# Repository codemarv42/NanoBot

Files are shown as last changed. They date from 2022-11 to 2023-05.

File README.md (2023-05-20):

# NanoBot

The NanoBot is basically a small robot, which was developed for educational purposes. It comes with a variety of sensors such as light sensors, color sensors, distance sensors and with the paired Jetson Nano from Nvidia with one or more cameras. In addition, you can connect even more modules and sensors through the extra pins, making the limits almost infinite. 

NanoBotRev1

# Hardware

The hardware of this project consists of a self-developed circuit board and 3D printed parts made of TPE 60A and PLA. 

## Short building instruction

### Note that only the first version of the NanoBot board works without problems, so it is not recommended to rebuild the latest version!

The assembly of the robot requires **extensive equipment and experience** in soldering SMD components. How you solder the components is up to you.

Recommended tools:

- Flat tip soldering iron
- Solder (0.8mm), flux
- Hotplate
- Hot air soldering station
- Solder paste (SnAg3Cu0.5)
- Tweezers, side cutter

The required components are listed in the Excel document in the hardware folder and are mostly from LCSC. The board itself can be produced by different manufacturers, for example JLCPCB. Simply upload the Gerber file and select the following parameters:

Parameter for PCB (NanoBot REV1):

- Layer: 2
- Thickness: 1,6mm / 2mm
- Length: 112.9mm
- Height: 100.8mm
- Minimum Copper Trace Width: 0.15mm

Parameter for PCB (NanoBot REV2):

- Layer: 2
- Thickness: 1,6mm / 2mm
- Length: 112.9mm
- Height: 100.8mm
- Minimum Copper Trace Width: 0.15mm

## 3D printed parts

For better light measurements, it is recommended to print out the three different light guards and attach them with superglue. Also, use TPE 60A for the tires, as this elastic material prevents the robot from slipping on the floor, unlike TPU.

Parts: 
- ***4x Flange coupling connector 3mm (not 3d printed!)***
- 4x Motor bracket PLA (40% infill)
- 1x light sensor protection Resin (Black)
- 2x Outer light sensor protection Resin (Black)
- 4x Tire TPE 60A
- 1x Rotary encoder knob TPU / TPE
- 4x Rim PLA

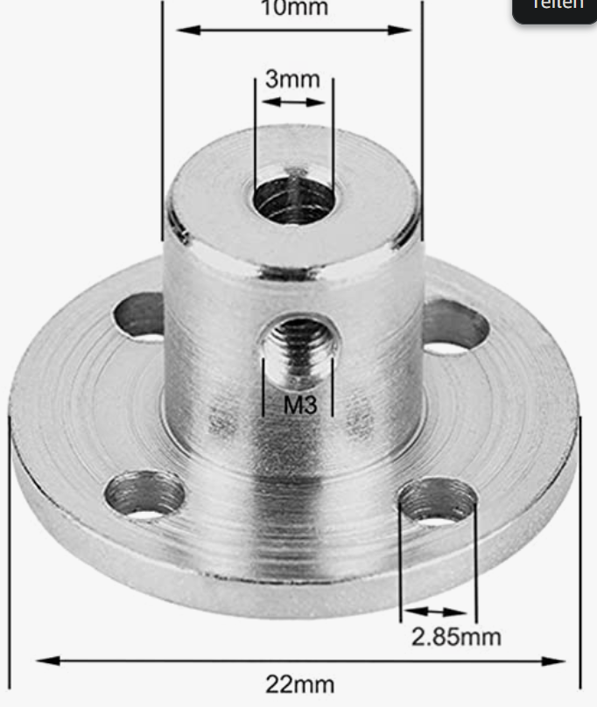
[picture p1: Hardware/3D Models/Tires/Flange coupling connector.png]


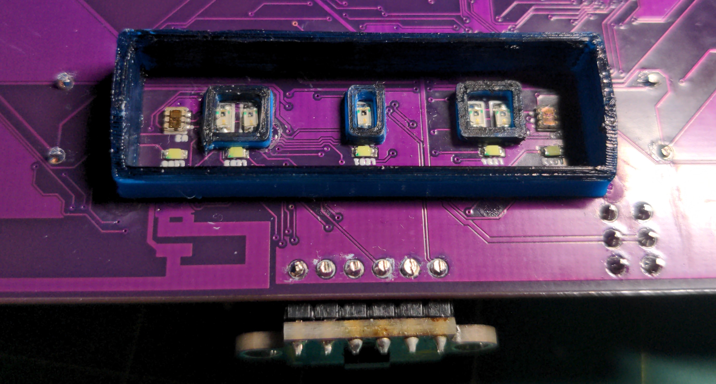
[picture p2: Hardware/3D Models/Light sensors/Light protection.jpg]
Light protector


## Improvements

> - [ ] Place light sensors in the center to increase maneuverability
> - [ ] Bigger Tires
> - [X] Better XT-30 position on the PCB
> - [X] More external ports
> - [X] Internal Li-Po charger, which draws power via USB-C PD
> - [X] Physical switch or MOSFET to disconnect the battery from the PCB
> - [X] Battery under discharge protection
> - [X] Additional light sensors on the outside of the PCB
> - [X] Constant motor voltage
> - [ ] Jetson Nano power supply with short circuit protection
> - [X] Material reflective sensor on the bottom
> - [X] Use Led with a wider spectrum
> - [X] Esd and insulation around gyro sensor
> - [ ] Reset button does not work
> - [X] Mounting holes next to the light sensor bar and the silver strip sensor

Nano Bot REV2

# Software

In my case, the robot is used to follow a line, avoid obstacles on the track and collect balls. These are the requirements for RoboCup in the Rescue Line division. However, depending on the requirements of the robot, the code will vary in your case. Therefore, this code serves mainly as a basis for your application. However, the code contains everything in the overall package to control and read out all sensors and peripherals. You can also reprogram the robot with Micro Python, because the processor (ESP32) allows it.

Required libraries:

- Adafruit_GFX.h - https://github.com/adafruit/Adafruit-GFX-Library
- Adafruit_SSD1306.h - https://github.com/adafruit/Adafruit_SSD1306
- ESP32_Servo.h - https://github.com/jkb-git/ESP32Servo
- MPU6050_light.h - https://github.com/rfetick/MPU6050_light
- CD74HC4067.h - https://github.com/waspinator/CD74HC4067
- VL53L1X.h - https://github.com/pololu/vl53l1x-arduino
- Adafruit_TCS34725.h - https://github.com/adafruit/Adafruit_TCS34725
- Adafruit_BusIO - https://github.com/adafruit/Adafruit_BusIO

## USB driver

In some cases, the USB controller is not automatically detected, which means that you have to install an additional driver:

- https://www.silabs.com/developers/usb-to-uart-bridge-vcp-drivers?tab=downloads

## Compilation settings

To compile your own program and then upload it to the NanoBot, some steps are necessary:

1. First you have to install the kernel of the ESP32 in Arduino: https://docs.espressif.com/projects/arduino-esp32/en/latest/installing.html
2. Next, the compilation settings must be specified. To do this, first select "ESP32 Dev Module" under Tools --> Board.
3. In the last step, the parameters of the ESP32 on the NanoBot must be set. To do this, select the following under Tools: 
- Board: "ESP32 Dev Module"
- Upload Speed: "921600"
- CPU Frequency: "240MHz (WiFi/BT)"
- Flash Frequency: "80MHz"
- Flash Mode: "QIO"
- Flash Size: "16MB (128Mb)" **4MB if you installed the W25Q32JVZPIQ Flash**
- Partition Scheme: "Minimal SPIFFS (1.9MB APP with OTA/190KB SPIFFS)" **for smaller code: Default**
- Programmer: "AVRISP mkll"
- Erase all flash: "Disabled"

## Improvements

> - [ ] Develop a communication protocol for the ESP32 and Jetson Nano via the I2C pin

## Flash BIN files to the robot

- Download the flash tool: https://www.espressif.com/en/support/download/other-tools
- Unzip the downloaded ZIP file and copy the selected BIN file into the bin folder contained in the unzipped file
- Start the exe file and select esp32
- Press the upper first box and then select the path of the bin file
- write next to the "@": 0x10000
- Then connect the robot to the pc and select the correct COM port (If the COM port is not displayed, install the driver)
- Click on start und press the boot button on the robot, if the upload does not start (If the boot button is not present, bridge the two pads with the name: "BOOT" and "GND")

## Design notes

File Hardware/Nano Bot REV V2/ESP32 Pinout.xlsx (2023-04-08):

GPIO | Input | Output | Belegt mit | Hinweis
0 | (OK) | (OK) | 0-BOOT | outputs PWM signal at boot
1 | X | (OK) | / | debug output at boot
2 | OK | OK | 2-P_ON | LED
3 | (OK) | X | / | HIGH at boot
4 | OK | OK | 4-S0
5 | OK | OK | 5-S1 | outputs PWM signal at boot
6 | X | X | / | connected to the integrated SPI flash
7 | X | X | / | connected to the integrated SPI flash
8 | X | X | / | connected to the integrated SPI flash
9 | X | X | / | connected to the integrated SPI flash
10 | X | X | / | connected to the integrated SPI flash
11 | X | X | / | connected to the integrated SPI flash
12 | (OK) | OK | 12-S2 | boot fail if pulled high
13 | OK | OK | 13-S3
14 | OK | OK | 14-CHARGE_STAT | outputs PWM signal at boot
15 | OK | OK | 15-ENC_SW | outputs PWM signal at boot
16 | OK | OK | 16
17 | OK | OK | 17-EN_RST
18 | OK | OK | 18-SERVO2
19 | OK | OK | 19-SERVO1
21 | OK | OK | 21-SDA
22 | OK | OK | 22-SCL
23 | OK | OK | 23-PWMA
25 | OK | OK | 25-PWMB
26 | OK | OK | 26-BUZZER
27 | OK | OK | 27-SHCP
32 | OK | OK | 32-STCP
33 | OK | OK | 33-DS
34 | OK | X | 34-ENC_B
35 | OK | X | 35-ENC_A
36 | OK | X | 36-VBAT | ADC
39 | OK | X | 39-VOUT | ADC

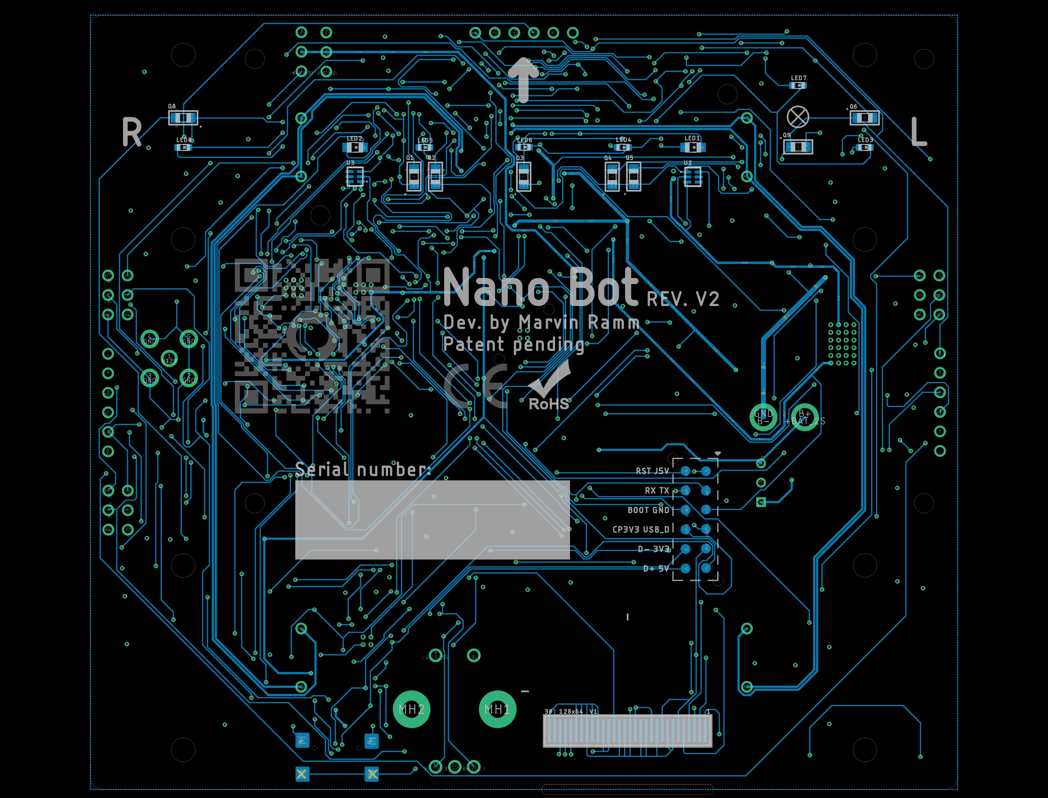
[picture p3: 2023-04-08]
Hardware/Nano Bot REV V2/NanoBot_6.png

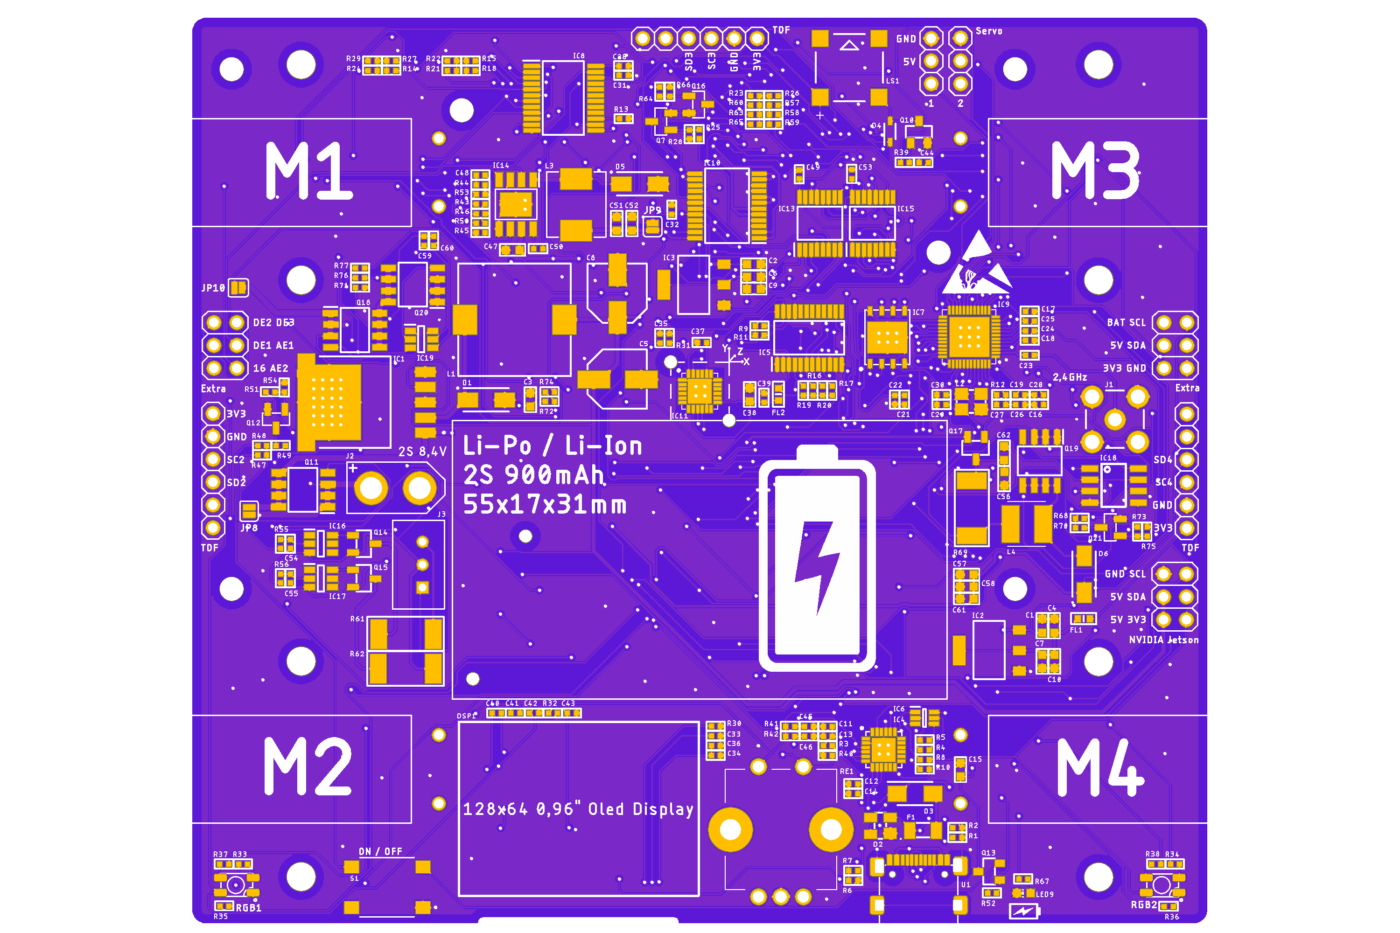
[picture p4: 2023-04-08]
Hardware/Nano Bot REV V2/NanoBot_1.png

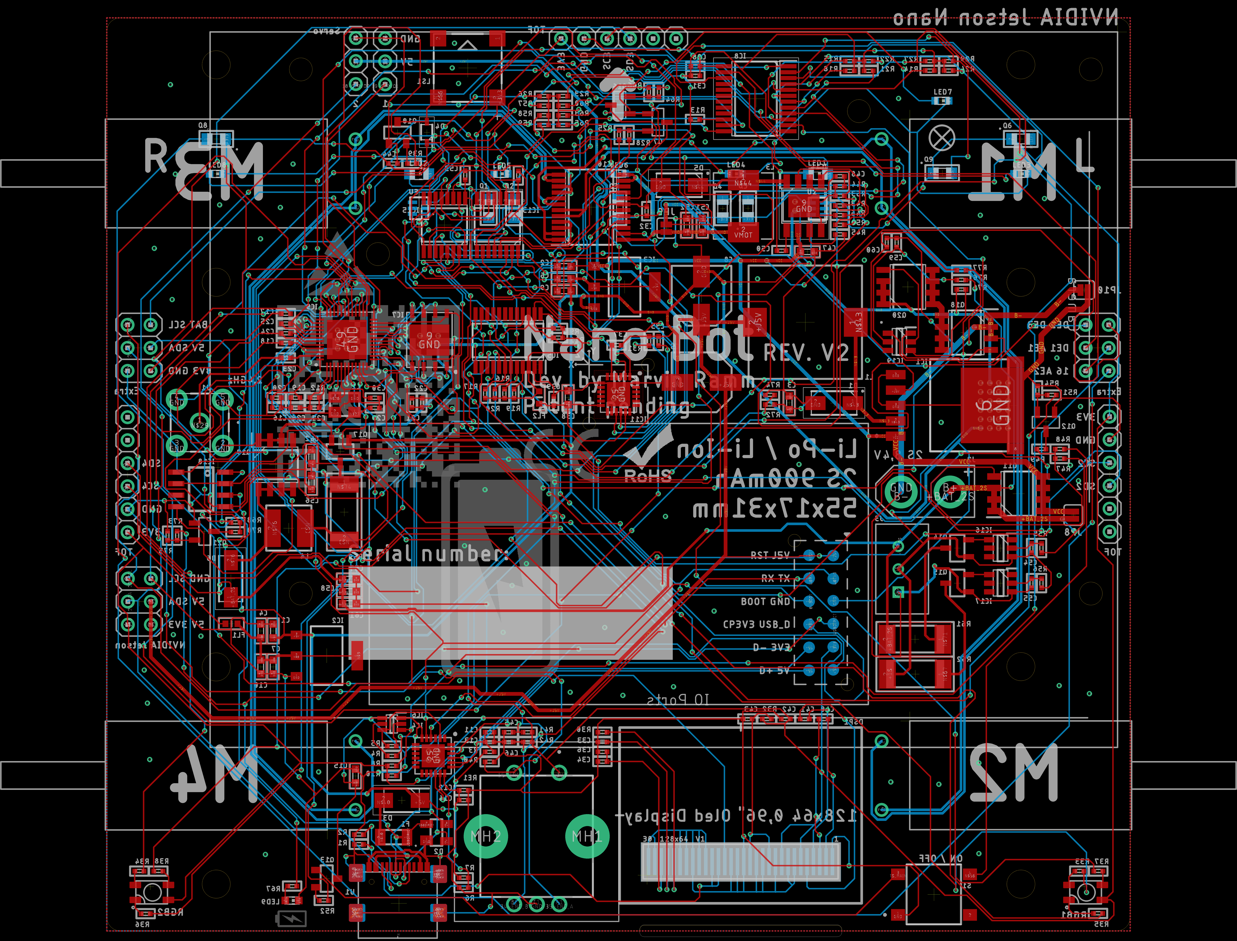
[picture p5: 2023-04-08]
Hardware/Nano Bot REV V2/NanoBot_4.png

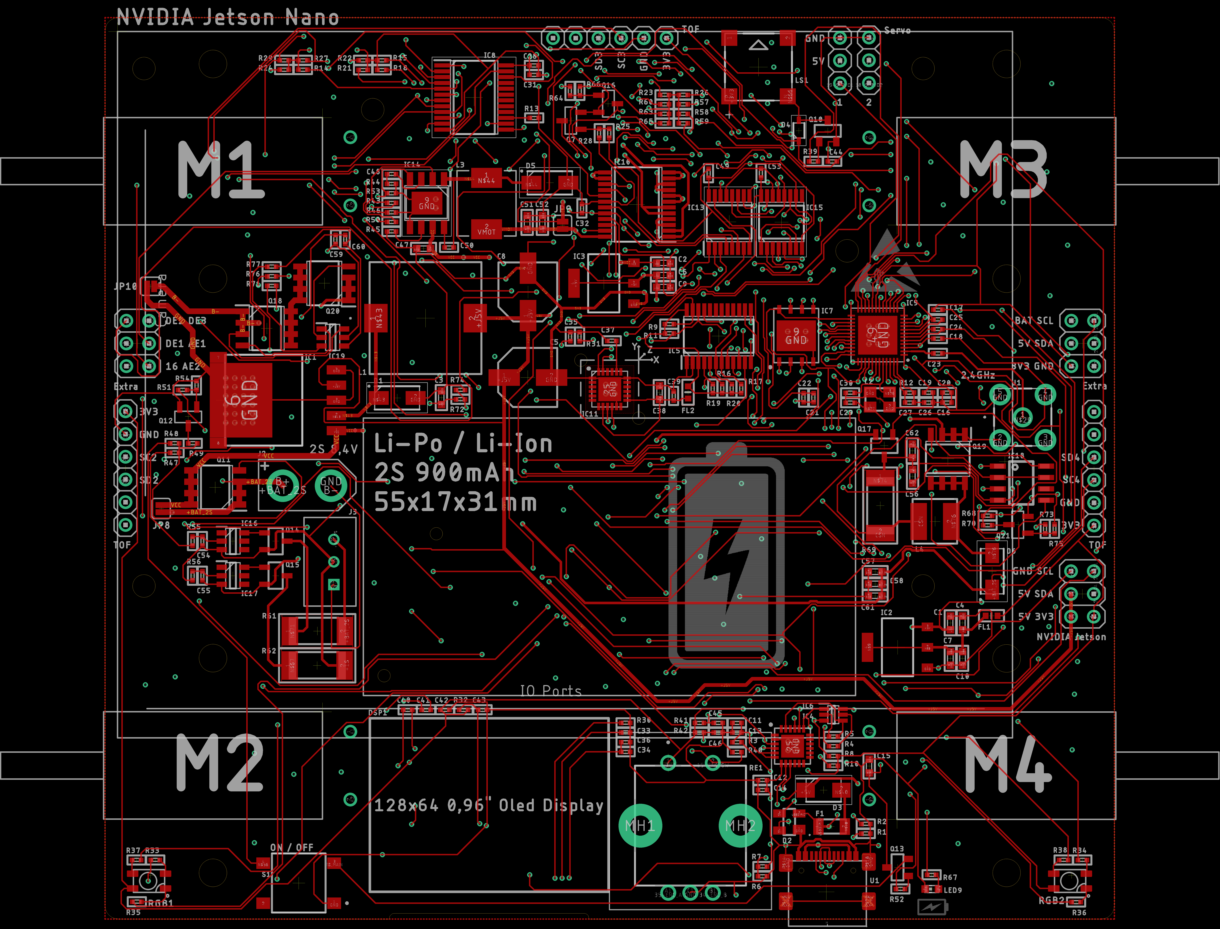
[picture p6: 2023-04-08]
Hardware/Nano Bot REV V2/NanoBot_5.png

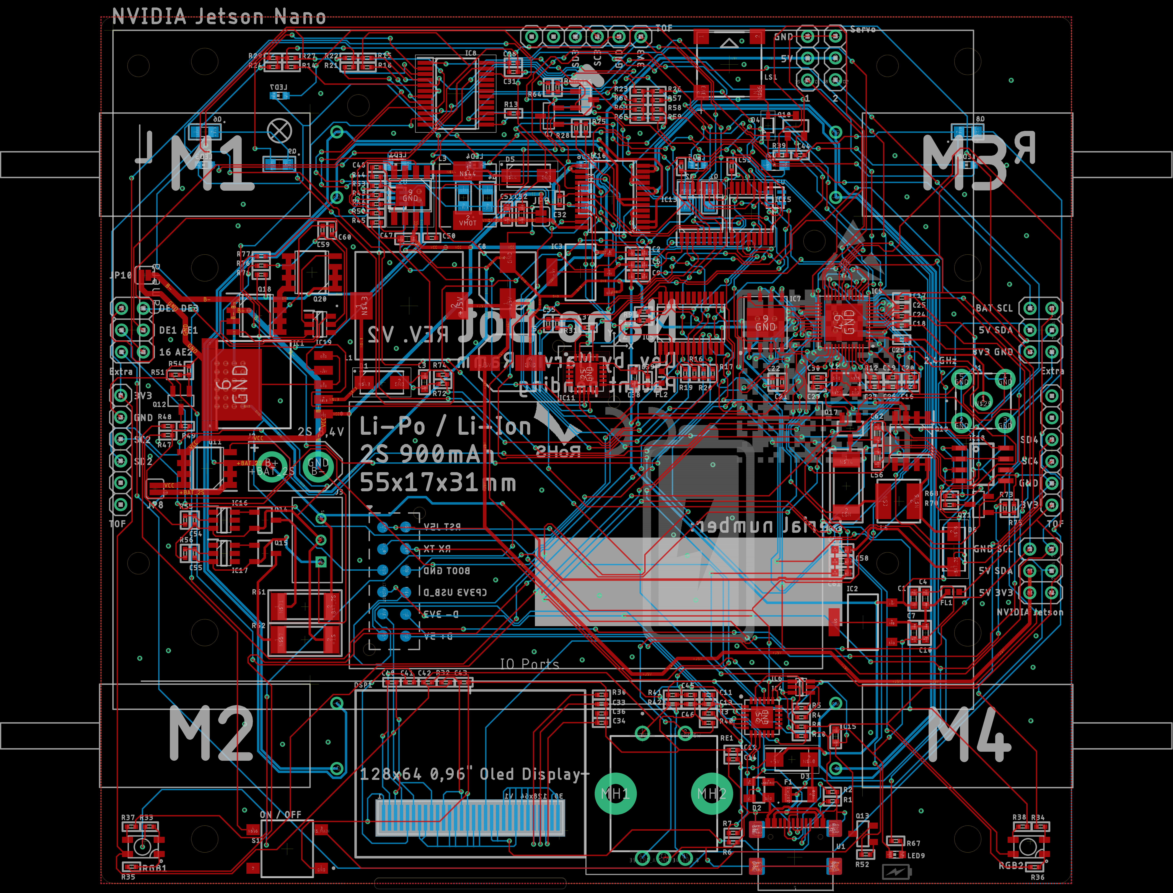
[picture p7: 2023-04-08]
Hardware/Nano Bot REV V2/NanoBot_3.png

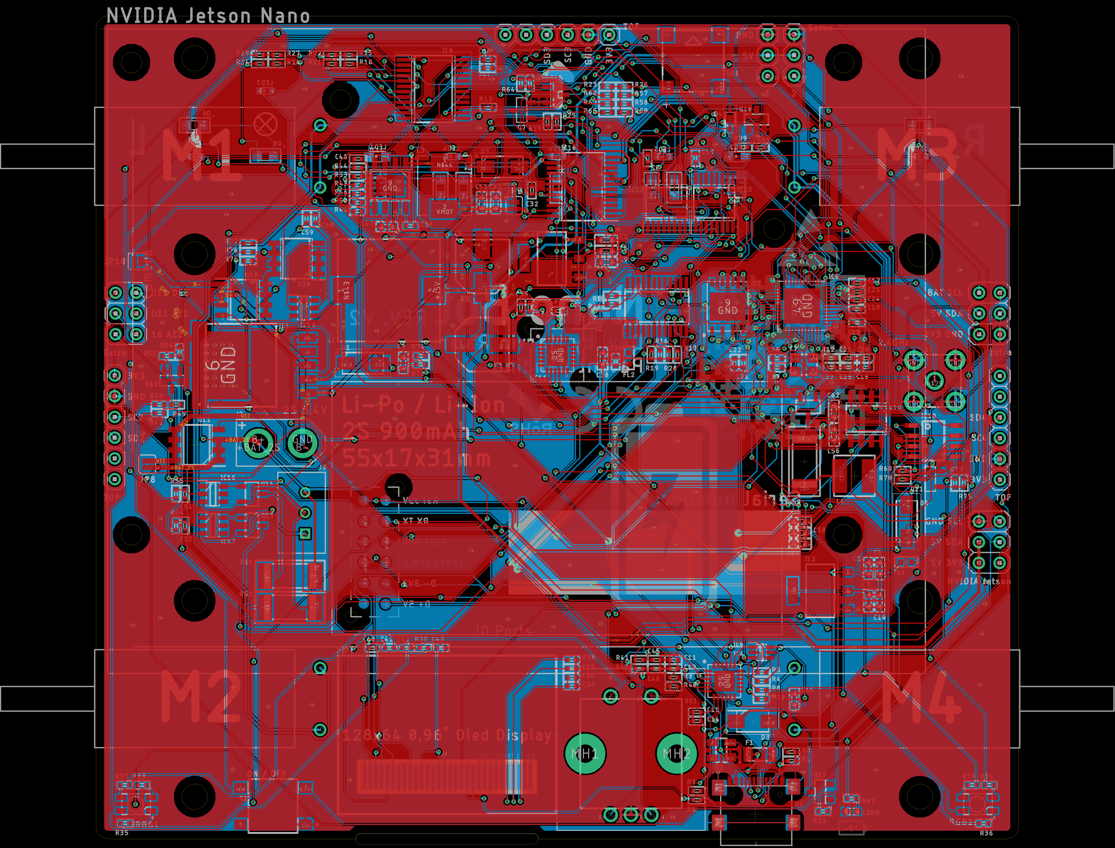
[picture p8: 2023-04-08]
Hardware/Nano Bot REV V2/NanoBot_7.png

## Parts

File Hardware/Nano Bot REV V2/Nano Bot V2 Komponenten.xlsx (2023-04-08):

Nano Bot V2 Komponenten
Reihe | Schaltplan Annotation(en) | Art | Hersteller Bezeichnung | LCSC Nummer | Anzahl | Preis pro Einheit | Gesamt | Hinweis | Link
1 | U1 | USB Connector | TYPE-C-31-M-31 | C2760486 | 1 | 0.2000 € | 0.2000 € | X | https://www.lcsc.com/product-detail/USB-Connectors_Korean-Hroparts-Elec-TYPE-C-31-M-31_C2760486.html
2 | F1 | 6V 1.5A 100A 3A 1206 Resettable Fuse | TLC-NSMD150 | C261956 | 1 | 0.0556 € | 0.0556 € | X | https://www.lcsc.com/product-detail/Resettable-Fuses_span-style-background-color-ff0-TLC-span-Electronic-TLC-NSMD150_C261956.html
3 | D3 | 30V 550mV@5A 5A DO-221AC Schottky Barrier Diode | SK53AFL-TP | C780074 | 1 | 0.1400 € | 0.1400 € | X
4 | D2 | ESD protection | SP0503BAHTG | C7074 | 1 | 0.1402 € | 0.1402 € | X | https://www.lcsc.com/product-detail/TVS_Littelfuse-SP0503BAHTG_C7074.html
5 | IC2 | Linear Voltage Regulators 1A 60dB@(120Hz) | AMS1117-3.3 | C347222 | 1 | 0.0402 € | 0.0402 € | X | https://www.lcsc.com/product-detail/Linear-Voltage-Regulators-LDO_UMW-Youtai-Semiconductor-Co-Ltd-AMS1117-3-3_C347222.html
6 | FL1, FL2 | 50mΩ ±25% 120Ω@100MHz 0603 Ferrite Beads ROHS | BLM18PG121SN1D | C14709 | 2 | 0.0067 € | 0.0134 € | X | https://www.lcsc.com/product-detail/Ferrite-Beads_Murata-Electronics-BLM18PG121SN1D_C14709.html
7 | IC3 | 1.4A Fixed 5V~5V Positive 18V SOT-223 Linear Voltage Regulators (LDO) ROHS | AMS1117-5.0 | C473812 | 1 | 0.0383 € | 0.0383 € | X | https://www.lcsc.com/product-detail/Linear-Voltage-Regulators-LDO_Slkor-SLKORMICRO-Elec-AMS1117-5-0_C473812.html
8 | D1, D5, D6 | 40V Single 500mV@3A 3A SMA(DO-214AC) Schottky Barrier Diodes (SBD) ROHS | SS34A | C2886580 | 3 | 0.0250 € | 0.0750 € | X | https://www.lcsc.com/product-detail/Schottky-Barrier-Diodes-SBD_Guangdong-Hottech-SS34A_C2886580.html
9 | IC1 | TO-263-5 DC-DC Converters ROHS | LM2576S-5.0 | C2920854 | 1 | 0.4800 € | 0.4800 € | X | https://www.lcsc.com/product-detail/DC-DC-Converters_Minos-LM2576S-5-0_C2920854.html
10 | IC5 | TSSOP-24 Signal Switches / Encoders & Decoders / Multiplexers ROHS | TCA9548APWR | C130026 | 1 | 0.7400 € | 0.7400 € | X | https://www.lcsc.com/product-detail/Signal-Switches-Encoders-Decoders-Multiplexers_Texas-Instruments-TCA9548APWR_C130026.html
11 | L1 | 1.9A 100uH ±20% SMD,12.5x12.5mm Power Inductors ROHS | SLF12575T-101M1R9-PF | C81470 | 1 | 0.5600 € | 0.5600 € | X | https://www.lcsc.com/product-detail/Power-Inductors_TDK-SLF12575T-101M1R9-PF_C81470.html
12 | IC4 | QFN-24-EP(4x4) USB ICs ROHS | CP2102N-A02-GQFN24R | C969151 | 1 | 4.1177 € | 4.1177 € | X | https://www.lcsc.com/product-detail/USB-ICs_SILICON-LABS-CP2102N-A02-GQFN24R_C969151.html
13 | IC6 | 40V 150mW 100@10mA,1V 200mA 2 NPN SC-88 Bipolar Transistors - BJT ROHS | LMBT3904DW1T1G | C131781 | 1 | 0.0213 € | 0.0213 € | X | https://www.lcsc.com/product-detail/Bipolar-Transistors-BJT_LRC-LMBT3904DW1T1G_C131781.html
14 | IC8 | SSOP-24-208mil Analog Switches / Multiplexers ROHS | CD74HC4067SM96 | C98457 | 1 | 0.7900 € | 0.7900 € | X | https://www.lcsc.com/product-detail/Analog-Switches-Multiplexers_Texas-Instruments-CD74HC4067SM96_C98457.html
15 | IC7 | WSON-8-EP(5x6) NOR FLASH ROHS | W25Q128JVPIQ | C2803379 | 1 | 1.4200 € | 1.4200 € | X | https://www.lcsc.com/product-detail/NOR-FLASH_Winbond-Elec-W25Q128JVPIQ_C2803379.html
16 | J1 | 1 Inner bore SMA Board Edge Positive foot 6GHz -65℃~+165℃ 50Ω 6.35mm Plugin RF Connectors / Coaxial Connectors ROHS | 5-1814832-2 | C482015 | 1 | 1.0500 € | 1.0500 € |  | https://www.lcsc.com/product-detail/RF-Connectors-Coaxial-Connectors_TE-Connectivity-5-1814832-2_C482015.html
17 | IC9 | QFN-48-EP(6x6) RF Transceiver ICs ROHS | ESP32-D0WDQ6 | C129733 | 1 | 1.8150 € | 1.8150 € |  | https://www.lcsc.com/product-detail/RF-Transceiver-ICs_Espressif-Systems-ESP32-D0WDQ6_C129733.html
18 | L2 | 40MHz 12pF ±10ppm SMD3225-4P Crystals ROHS | S3240000121040 | C426989 | 1 | 0.0600 € | 0.0600 € | X | https://www.lcsc.com/product-detail/Crystals_JGHC-S3240000121040_C426989.html
19 | Q1, Q2, Q3, Q4, Q5, Q6, Q8, Q9 | 20mA NPN 30V 100nA 940nm 0805 Phototransistors ROHS | PT17-21C/L41/TR8 | C100090 | 8 | 0.0587 € | 0.4696 € | X | https://www.lcsc.com/product-detail/Phototransistors_Everlight-Elec-PT17-21C-L41-TR8_C100090.html
20 | U2, U3 | Ambient Light Sensors ROHS | TCS34725FN | C2649487 | 2 | 2.5000 € | 5.0000 € | X | https://www.lcsc.com/product-detail/Ambient-Light-Sensors_Advanced-Monolithic-Systems-TCS34725FN_C2649487.html
21 | Q7, Q12, Q16, Q21 | 20V 2.9A 57mΩ@4.5V,3.6A 710mW N Channel SOT-23 MOSFETs ROHS | SI2302DDS-T1-GE3 | C194092 | 4 | 0.4300 € | 1.7200 € | X | https://www.lcsc.com/product-detail/MOSFETs_Vishay-Intertech-SI2302DDS-T1-GE3_C194092.html
22 | LED1, LED2 | 2600K~3200K 正贴 White light 80mW 0805 Light Emitting Diodes (LED) ROHS | BZ-C0805-W2-E1 | C2833071 | 2 | 0.0190 € | 0.0380 € |  | https://www.lcsc.com/product-detail/Light-Emitting-Diodes-LED_baizou-BZ-C0805-W2-E1_C2833071.html
23 | IC10 | 1A Brush DC Motor 2.7V~5.5V Parallel SSOP-24 Motor Driver ICs ROHS | TB6612FNG,C,8,EL | C141517 | 1 | 2.2300 € | 2.2300 € | X | https://www.lcsc.com/product-detail/Motor-Driver-ICs_TOSHIBA-TB6612FNG-C-8-EL_C141517.html
24 | IC11 | QFN-24-EP(4x4) Attitude Sensor/Gyroscope ROHS | MPU-6050 | C24112 | 1 | 7.2600 € | 7.2600 € | X | https://www.lcsc.com/product-detail/Attitude-Sensor-Gyroscope_TDK-InvenSense-MPU-6050_C24112.html
25 | RGB1, RGB2 |  |  |  | 2 |  | 0.0000 € | X
26 | RE1 | Plugin Rotary Encoders ROHS | PEC12R-4120F-S0012 | C143801 | 1 | 1.4700 € | 1.4700 € | X | https://www.lcsc.com/product-detail/Rotary-Encoders_BOURNS-PEC12R-4120F-S0012_C143801.html
27 | LS1 | Externally Driven 85dB@3.6V,10cm Magnetic 3.6V 2731Hz SMD,7.5x7.5mm Buzzers ROHS | KLJ-7525-3627 | C189208 | 1 | 0.4700 € | 0.4700 € | X | https://www.lcsc.com/product-detail/Buzzers_KELIKING-KLJ-7525-3627_C189208.html
28 | D4 | 100V 400mW Single 1.25V@150mA 8ns 300mA SOD-323 Switching Diode ROHS | 1N4148WS | C917117 | 1 | 0.0070 € | 0.0070 € | X | https://www.lcsc.com/product-detail/Switching-Diode_JSMSEMI-1N4148WS_C917117.html
29 | Q10, Q13 | 40V 200mW 100@10mA,1V 200mA NPN SOT-23 Bipolar Transistors - BJT ROHS | MMBT3904 | C181119 | 2 | 0.0063 € | 0.0126 € | X | https://www.lcsc.com/product-detail/Bipolar-Transistors-BJT_Guangdong-Hottech-MMBT3904_C181119.html
30 | IC13, IC15 | 2V~6V 串行至串行或并行 TSSOP-16 Shifting Register ROHS | 74HC595PW,118 | C5948 | 2 | 0.1635 € | 0.3270 € | X | https://www.lcsc.com/product-detail/Shifting-Register_Nexperia-74HC595PW-118_C5948.html
31 | Q11 | SOP-8 MOSFETs ROHS | IRF7416TRPBF | C5350823 | 1 | 0.2400 € | 0.2400 € |  | https://www.lcsc.com/product-detail/MOSFETs_TECH-PUBLIC-IRF7416TRPBF_C5350823.html
32 | S1 | 50mA SPST 24V SMD-4P,6x6.6mm Tactile Switches ROHS | B3S-1002P | C271751 | 1 | 0.4200 € | 0.4200 € |  | https://www.lcsc.com/product-detail/Tactile-Switches_Omron-Electronics-B3S-1002P_C271751.html
33 | IC14 |  | MP1584EN-LF-Z |  | 1 |  | 0.0000 € | X
34 | L3 | 8.8A 4.7uH ±20% 8.8A 20.8mΩ SMD,6.6x7.3mm Inductors (SMD) ROHS | MDA7050-4R7M | C2847541 | 1 | 0.8700 € | 0.8700 € | X | https://www.lcsc.com/product-detail/Inductors-SMD_KOHERelec-MDA7050-4R7M_C2847541.html
35 | LED3, LED4, LED5, LED6, LED7, LED8 | White light 100mW 0603 Light Emitting Diodes (LED) ROHS | SZYY0603W | C434422 | 6 | 0.0121 € | 0.0726 € | X | https://www.lcsc.com/product-detail/Light-Emitting-Diodes-LED_Yongyu-Photoelectric-SZYY0603W_C434422.html
36 | Q14, Q15 | 20V 2.5A 1000mW 55mΩ@4.5V,3.6A N Channel SOT-23 MOSFETs ROHS | FSS2302S | C2926140 | 2 | 0.0125 € | 0.0250 € | X | https://www.lcsc.com/product-detail/MOSFETs_FOSAN-FSS2302S_C2926140.html
37 | IC16, IC17 | SOT-23-6 Battery Management ICs ROHS | HY2213-BB3A | C113632 | 2 | 0.1171 € | 0.2342 € | X | https://www.lcsc.com/product-detail/Battery-Management-ICs_HYCON-Tech-HY2213-BB3A_C113632.html
38 | J2 | Power Connectors ROHS | XT30U-M | C99101 | 1 | 0.2100 € | 0.2100 € | X | https://www.lcsc.com/product-detail/Power-Connectors_Changzhou-Amass-Elec-XT30U-M_C99101.html
39 | Q18, Q20, Q19 | 30V 13A 3.1W 11.5mΩ@10V,12A N Channel SOIC-8 MOSFETs ROHS | AO4406AL | C35349 | 3 | 0.1500 € | 0.4500 € |  | https://www.lcsc.com/product-detail/MOSFETs_Alpha-Omega-Semicon-AO4406AL_C35349.html
40 | IC19 | SOT-23-6 Battery Management ICs ROHS | HY2120-CB | C116509 | 1 | 0.2480 € | 0.2480 € |  | https://www.lcsc.com/product-detail/Battery-Management-ICs_HYCON-Tech-HY2120-CB_C116509.html
41 | Q17 | SOT-23-3L MOSFETs ROHS | AO3407A | C5379096 | 1 | 0.0356 € | 0.0356 € | X | https://www.lcsc.com/product-detail/MOSFETs_MSKSEMI-AO3407A_C5379096.html
42 | L4 | 1.6A 10uH ±20% 2A 106mΩ SMD,5x5mm Inductors (SMD) ROHS | LQH5BPB100MT0L | C521243 | 1 | 0.2500 € | 0.2500 € |  | https://www.lcsc.com/product-detail/Inductors-SMD_Murata-Electronics-LQH5BPB100MT0L_C521243.html
43 | IC18 | SOP-8 Battery Management ICs ROHS | CN3302 | C559039 | 1 | 0.1500 € | 0.1500 € |  | https://www.lcsc.com/product-detail/Battery-Management-ICs_ShangHai-Consonance-Elec-CN3302_C559039.html
44 | LED9 | red led 0603 |  |  | 1 |  | 0.0000 € | X
 |  | Resistors
45 | R1, R2, R14, R15, R18, R21, R22, R24, R27 | 5,1kΩ 0402 |  |  | 9 |  | 0.0000 € | X
46 | R9, R11, R4, R5, R10, R8, R13, R19, R16, R20, R17, R31, R32, R40, R41, R42, R50 | 10kΩ 0402 |  |  | 17 |  | 0.0000 € | X
47 | R3, R29, R33, R35, R37, R34, R36, R38, R71, R67 | 2,2kΩ 0402 |  |  | 10 |  | 0.0000 € | X
48 | R7 | 22kΩ 0402 |  |  | 1 |  | 0.0000 € | X
49 | R6 | 33kΩ 0402 |  |  | 1 |  | 0.0000 € | X
50 | R12 | 20kΩ 0402 |  |  | 1 |  | 0.0000 € | X
51 | R23, R26, R57, R58, R59, R60, R63, R65, R55, R56 | 100Ω 0402 |  |  | 10 |  | 0.0000 € | X
52 | R25, R39, R48, R49, R51, R52, R64, R70, R73 | 1kΩ 0402 |  |  | 9 |  | 0.0000 € | X
53 | R28, R47, R54, R46, R43, R44, R45, R66, R72, R68, R75 | 100kΩ 0402 |  |  | 11 |  | 0.0000 € | X
54 | R30 | 390kΩ 0402 |  |  | 1 |  | 0.0000 € | X
55 | R53 | 75kΩ 0402 |  |  | 1 |  | 0.0000 € | X
56 | R61, R62 | 62Ω 2512 |  |  | 2 |  | 0.0000 € | X
57 | R76, R77 | 330Ω 0402 |  |  | 2 |  | 0.0000 € | X
58 | R74 | 64,9kΩ 0402 |  |  | 1 |  | 0.0000 € | X
59 | R69 | 0,1Ω 2512 |  |  | 1 |  | 0.0000 € | X
 |  | Capacitors
60 | C1, C2 | 4,7uF 0603 16V |  |  | 2 |  | 0.0000 € | X
61 | C4, C7, C15, C6, C9, C3, C15, C38, C47, C51, C52, C62, C56, C57, C58, C61 | 10uF 0603 16V |  |  | 16 |  | 0.0000 € | X
62 | C5, C8 | 150uF 16V ±20% SMD,D6.3xL7.7mm Aluminum Electrolytic Capacitors - SMD ROHS | UUD1C151MCL1GS | C445270 | 2 | 0.1920 € | 0.3840 € | X | https://www.lcsc.com/product-detail/Aluminum-Electrolytic-Capacitors-SMD_Nichicon-UUD1C151MCL1GS_C445270.html
63 | C11, C12, C28, C22, C17, C19, C18, C20, C32, C35, C49, C53, C50, C54, C55, C59, C60 | 0,1uF 0402 16V |  |  | 17 |  | 0.0000 € | X
64 | C13, C14 | 4,7uF 0402 6,3V |  |  | 2 |  | 0.0000 € | X
65 | C29, C30 | 12pF 0402 |  |  | 2 |  | 0.0000 € | X
66 | C27 | 3nF 0402 |  |  | 1 |  | 0.0000 € | X
67 | C26, C37, C45, C46 | 10nF 0402 |  |  | 4 |  | 0.0000 € | X
68 | C23 | 5,6pF 0402 |  |  | 1 |  | 0.0000 € | X
69 | C24, C25 | 270pF 0420 |  |  | 2 |  | 0.0000 € | X
70 | C21, C31, C39, C33, C34, C36, C40, C41, C42, C43, C44 | 1uF 0402 16V |  |  | 11 |  | 0.0000 € | X
71 | C16, C48 | 100pF 0402 |  |  | 2 |  | 0.0000 € | X

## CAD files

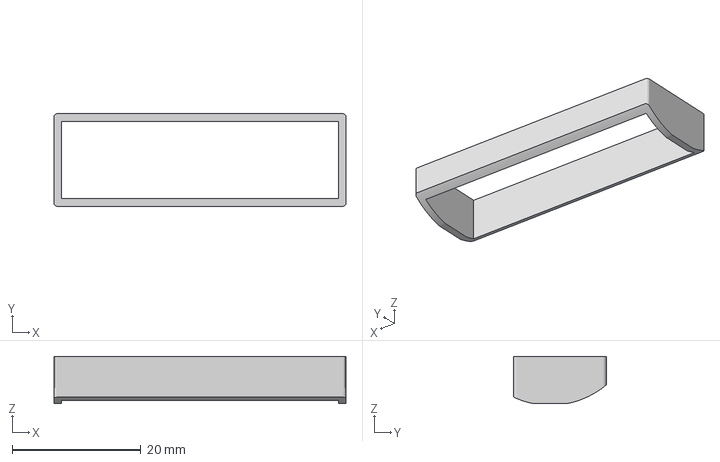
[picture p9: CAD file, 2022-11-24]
Hardware/3D Models/Light sensors/LargeLightProtection.3mf
45.4 x 14.4 x 7.32 mm

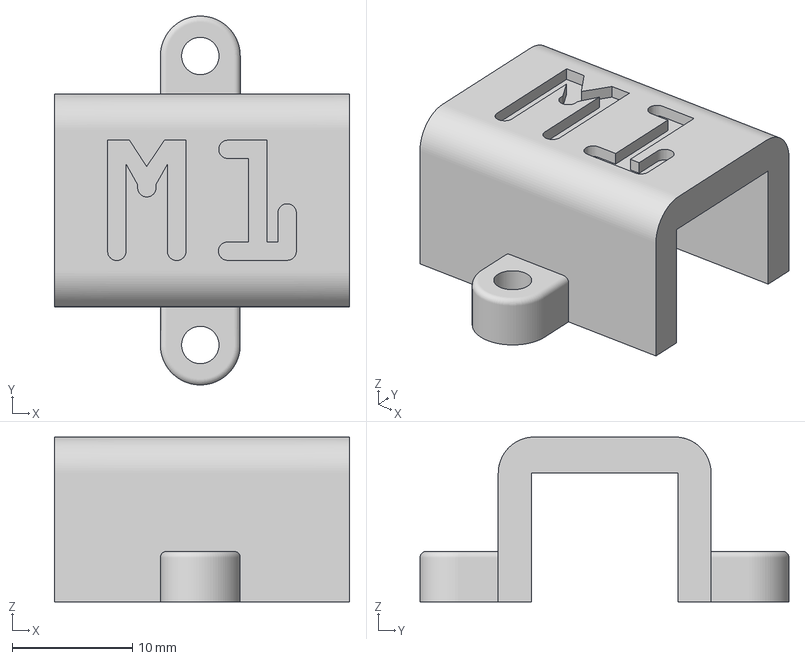
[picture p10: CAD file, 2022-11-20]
Hardware/3D Models/Motors/MotorHalterungM1.3mf
24.5 x 30.6 x 13.7 mm

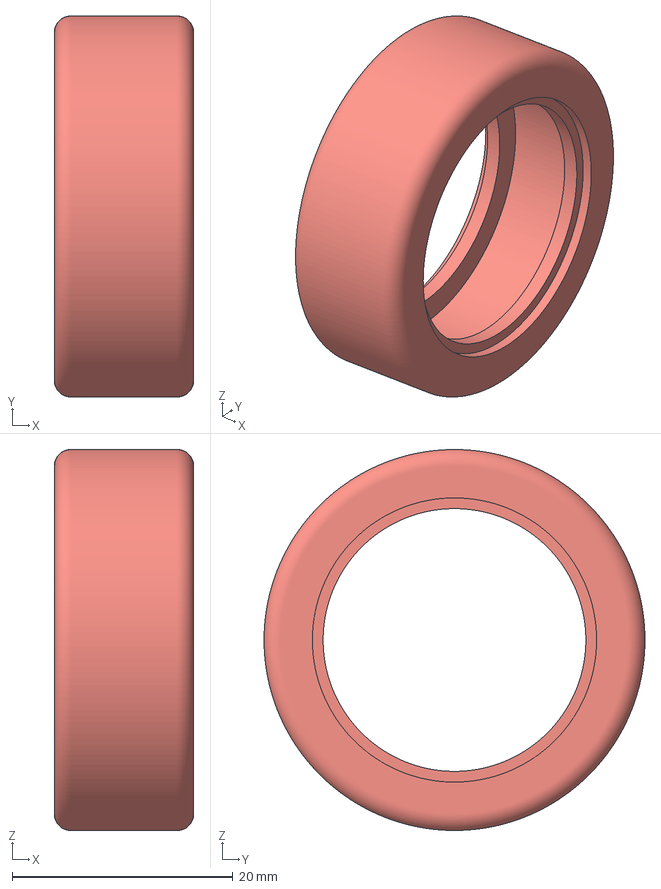
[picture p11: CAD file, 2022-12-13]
Hardware/3D Models/Tires/Tire_V2.3mf
12.6 x 34.5 x 34.5 mm

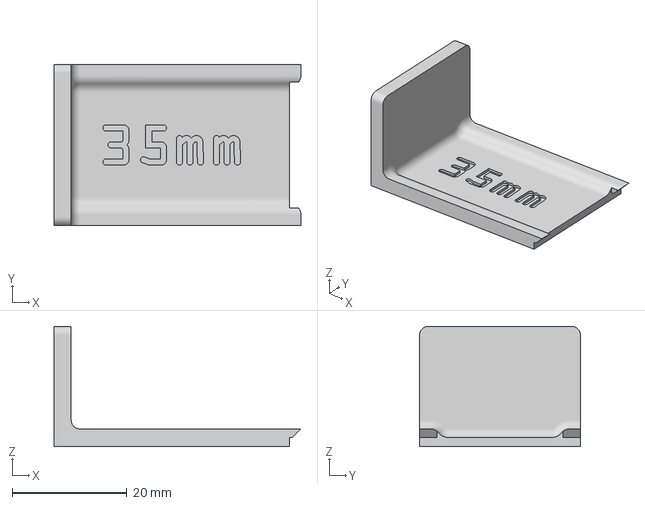
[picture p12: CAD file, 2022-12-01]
Hardware/3D Models/TOF Calibration.3mf
43.0 x 28.0 x 20.9 mm

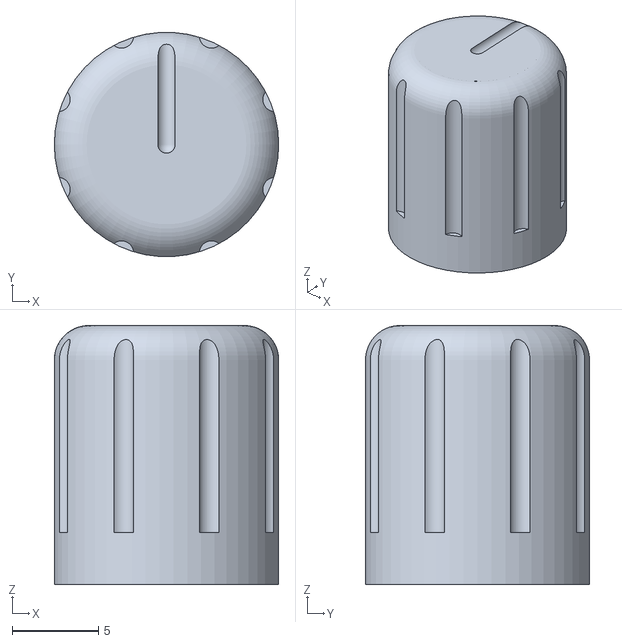
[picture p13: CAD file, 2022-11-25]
Hardware/3D Models/knob.stl
13.0 x 13.0 x 15.0

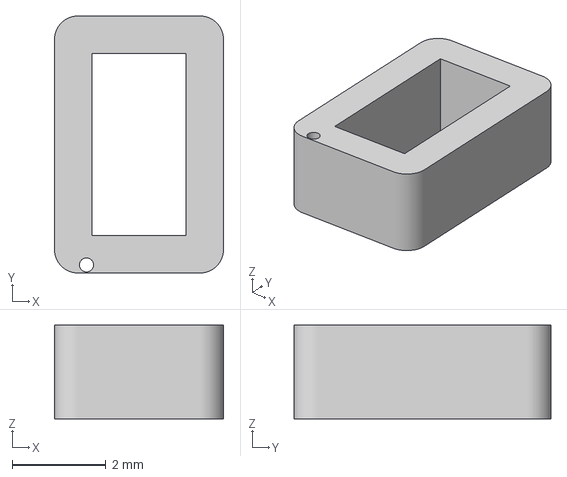
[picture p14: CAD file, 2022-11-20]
Hardware/3D Models/Light sensors/SingleLichtschutz.3mf
3.61 x 5.49 x 2.00 mm

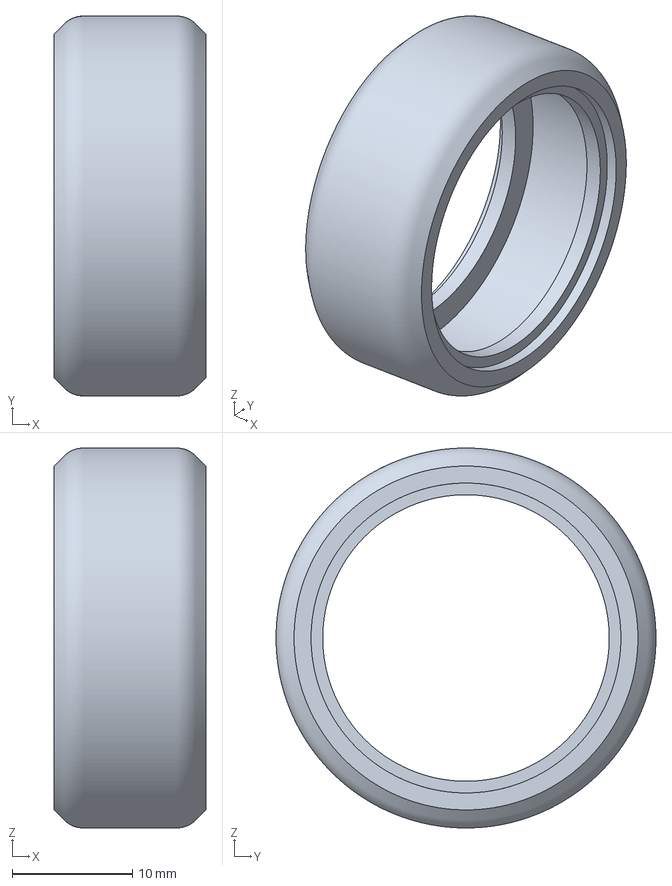
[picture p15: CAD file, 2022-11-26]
Hardware/3D Models/Tires/Reifen indoor.3mf
12.6 x 31.6 x 31.6 mm

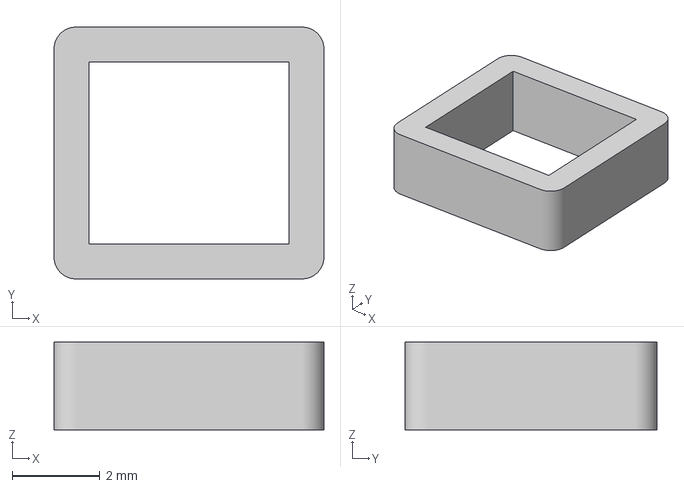
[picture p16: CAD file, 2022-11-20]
Hardware/3D Models/Light sensors/DualLichtschutz.3mf
6.16 x 5.75 x 2.00 mm

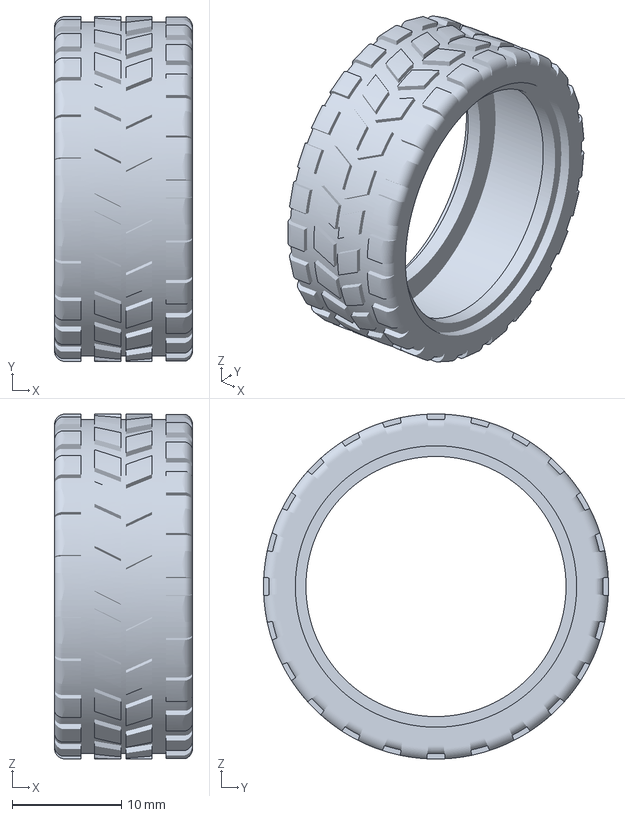
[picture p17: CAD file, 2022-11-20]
Hardware/3D Models/Tires/Reifen.3mf
12.6 x 31.6 x 31.6 mm

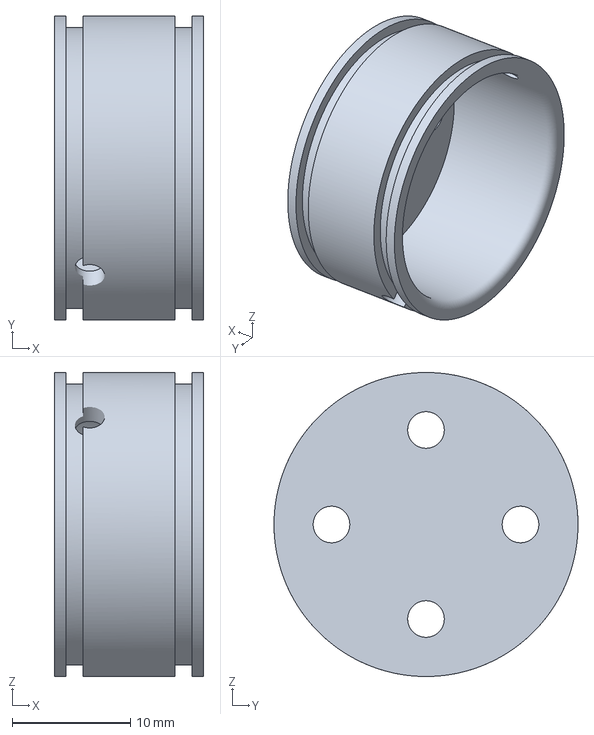
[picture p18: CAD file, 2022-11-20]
Hardware/3D Models/Tires/Felge.3mf
12.6 x 25.7 x 25.7 mm

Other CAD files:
Hardware/3D Models/Motors/MotorHalterungM3.3mf
Hardware/3D Models/Motors/MotorHalterungM4.3mf
Hardware/3D Models/Motors/MotorHalterungM2.3mf

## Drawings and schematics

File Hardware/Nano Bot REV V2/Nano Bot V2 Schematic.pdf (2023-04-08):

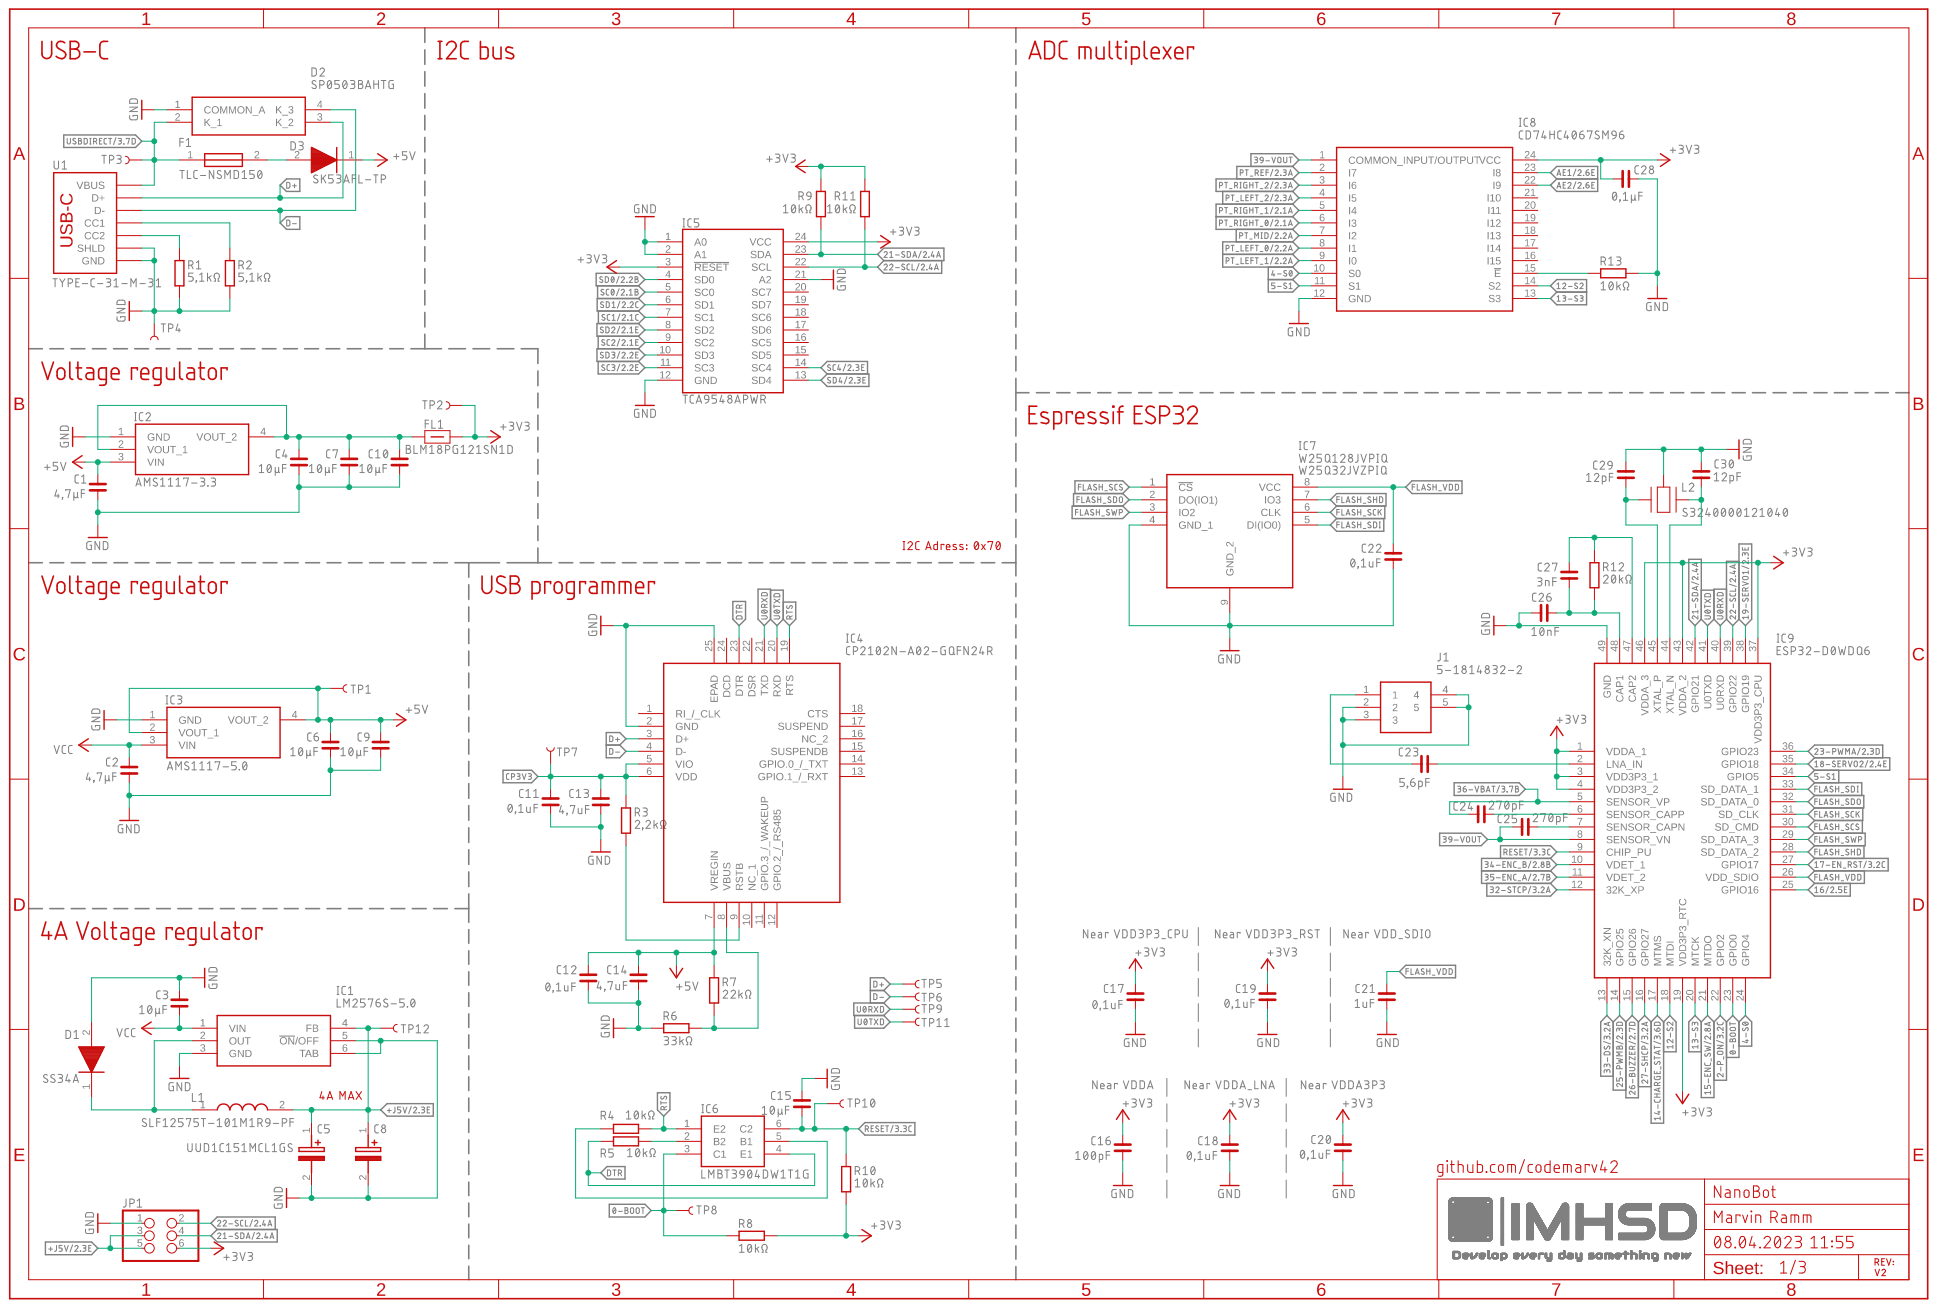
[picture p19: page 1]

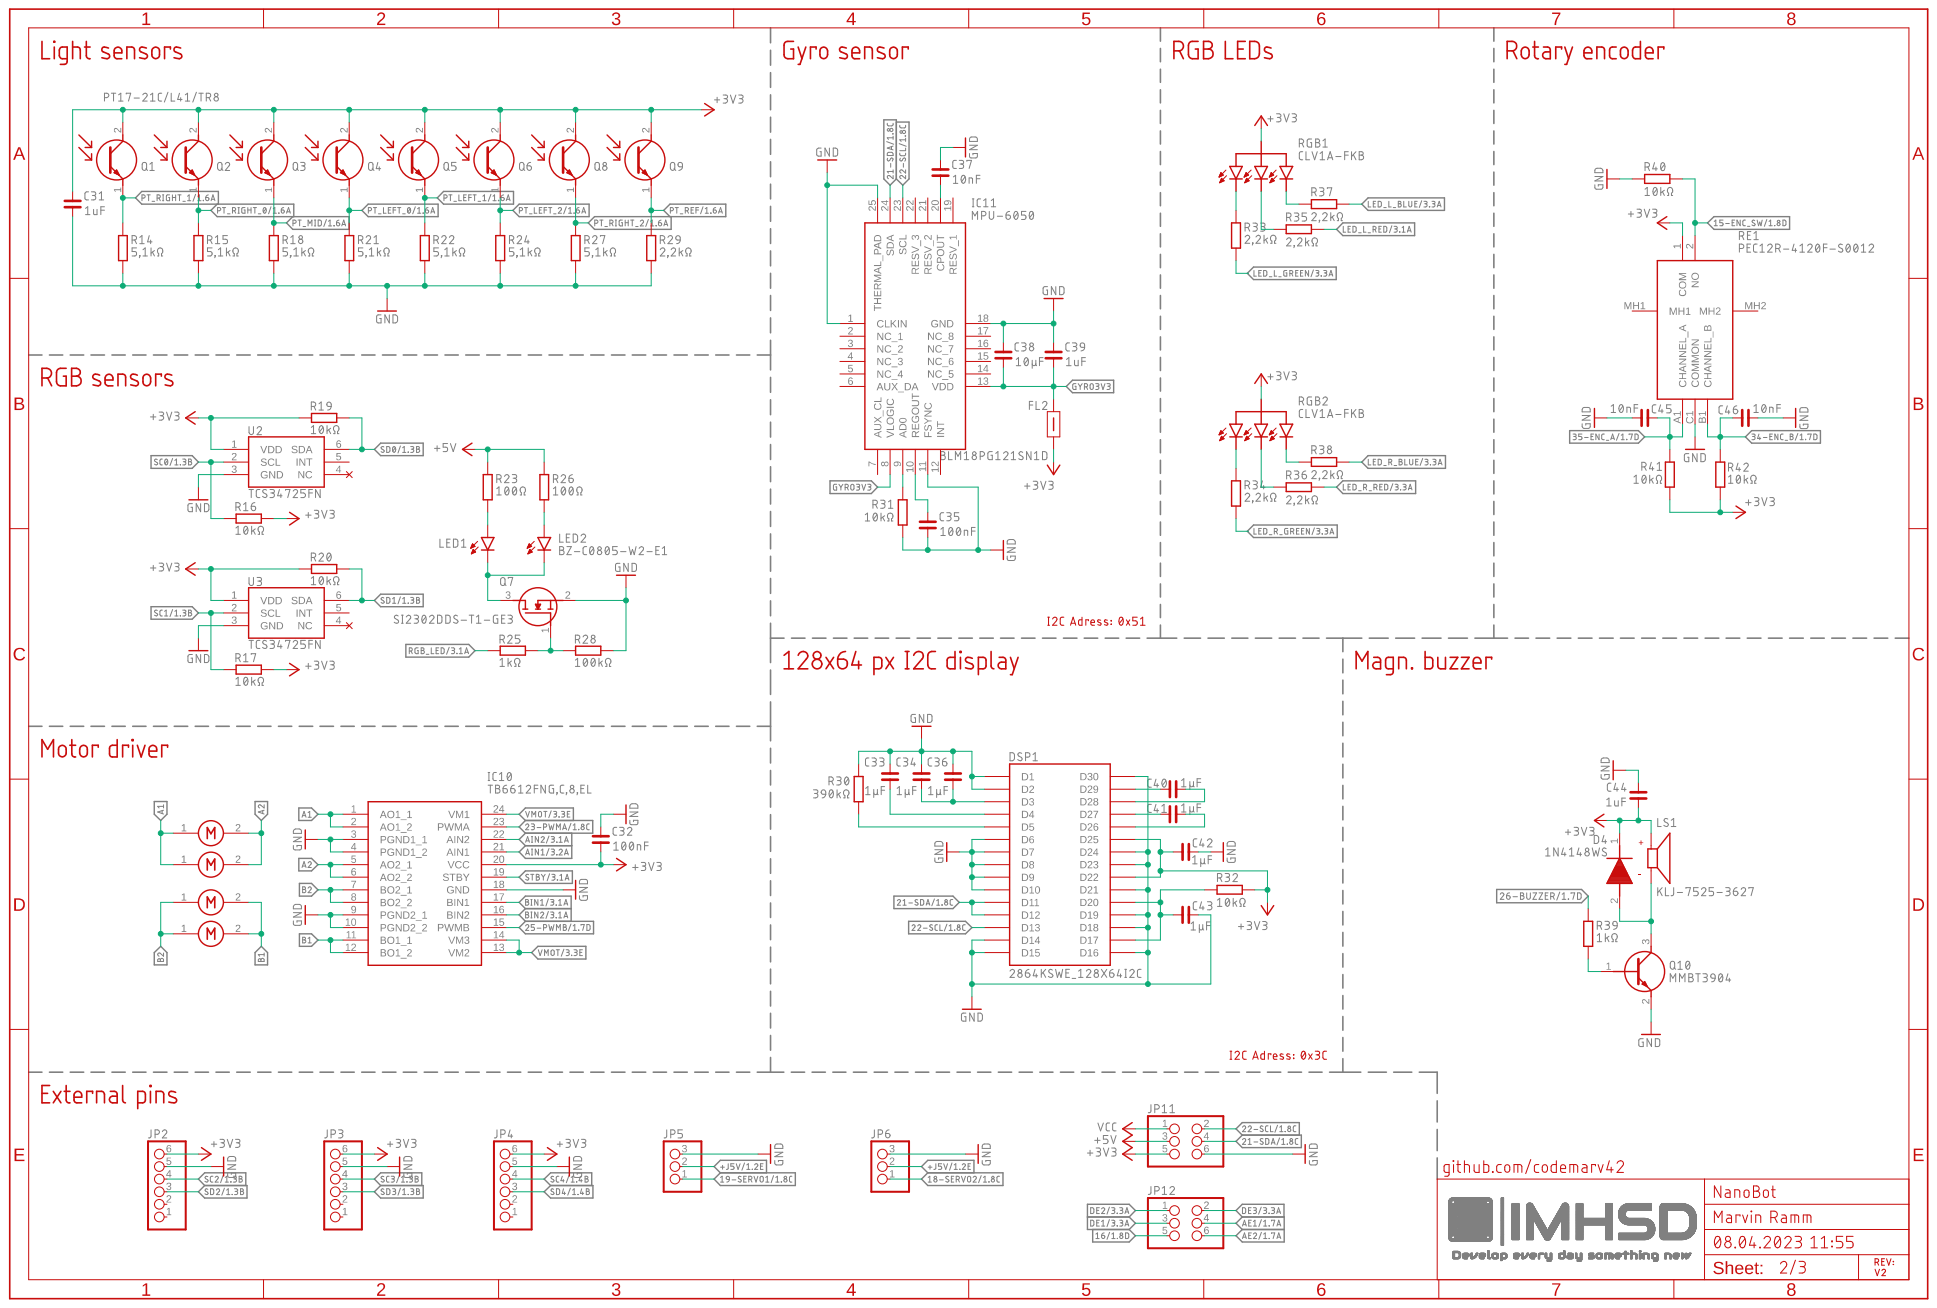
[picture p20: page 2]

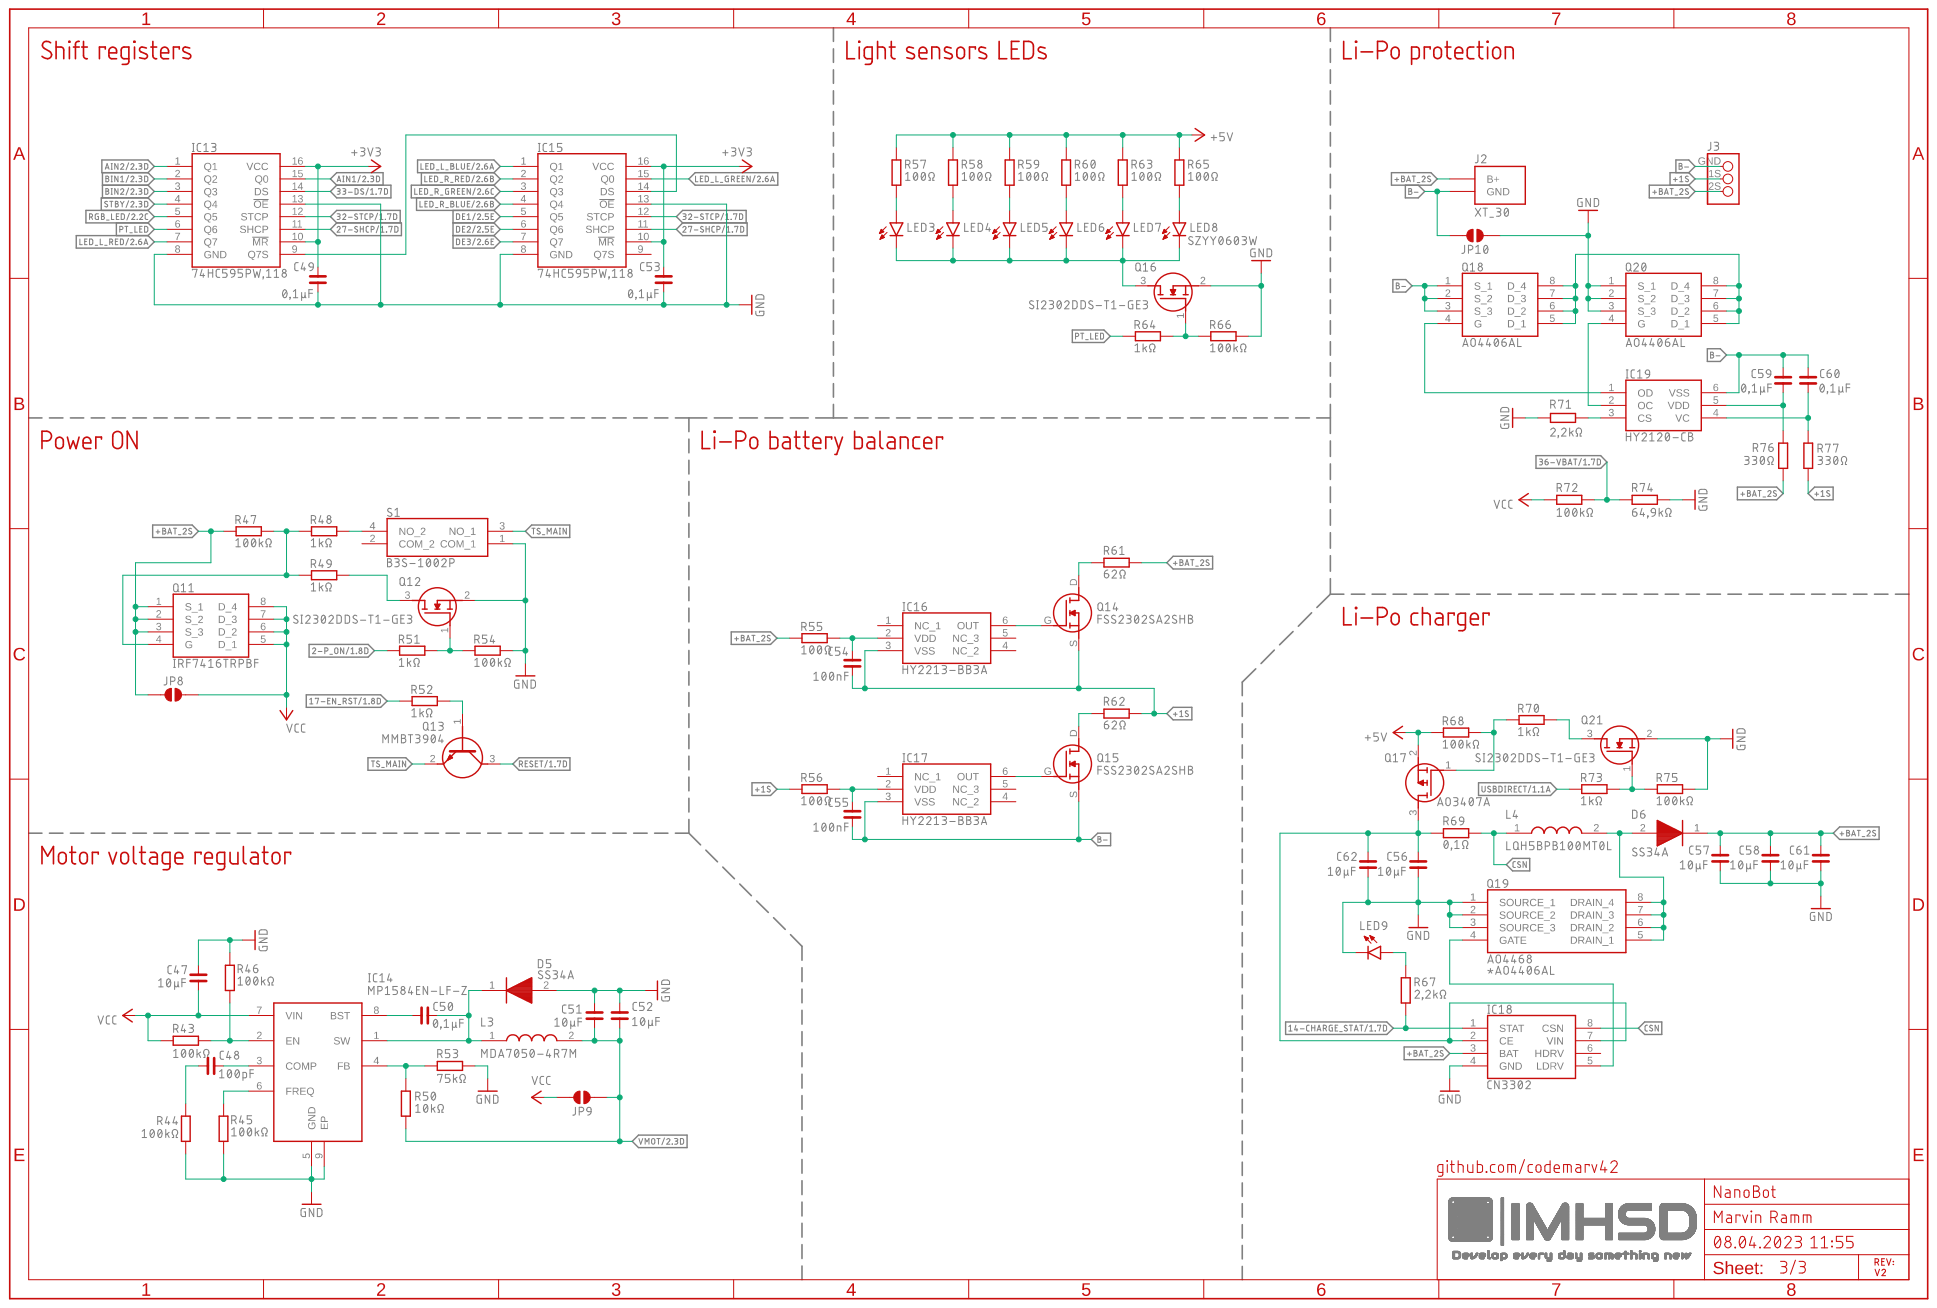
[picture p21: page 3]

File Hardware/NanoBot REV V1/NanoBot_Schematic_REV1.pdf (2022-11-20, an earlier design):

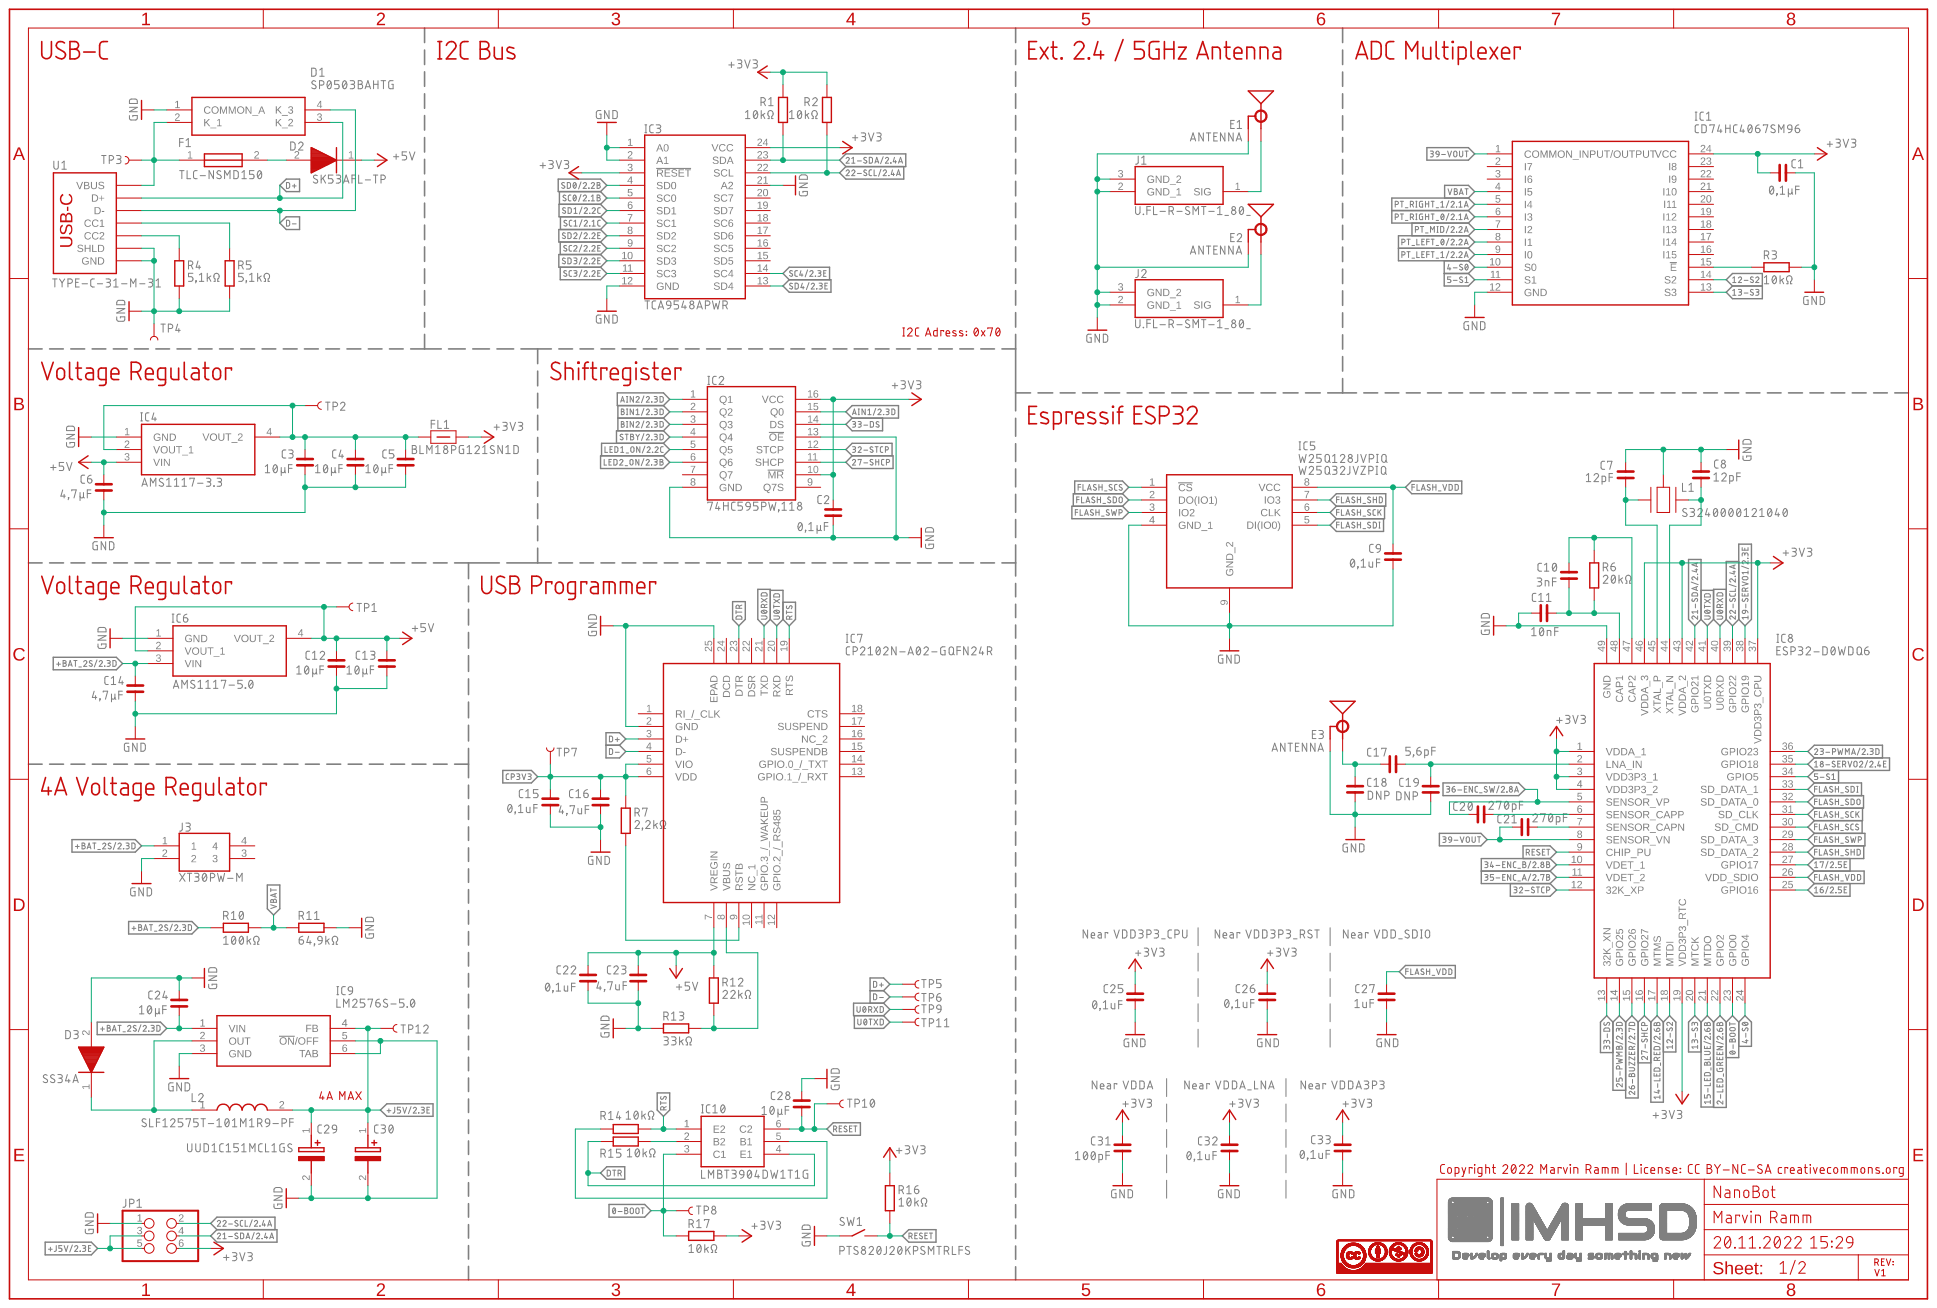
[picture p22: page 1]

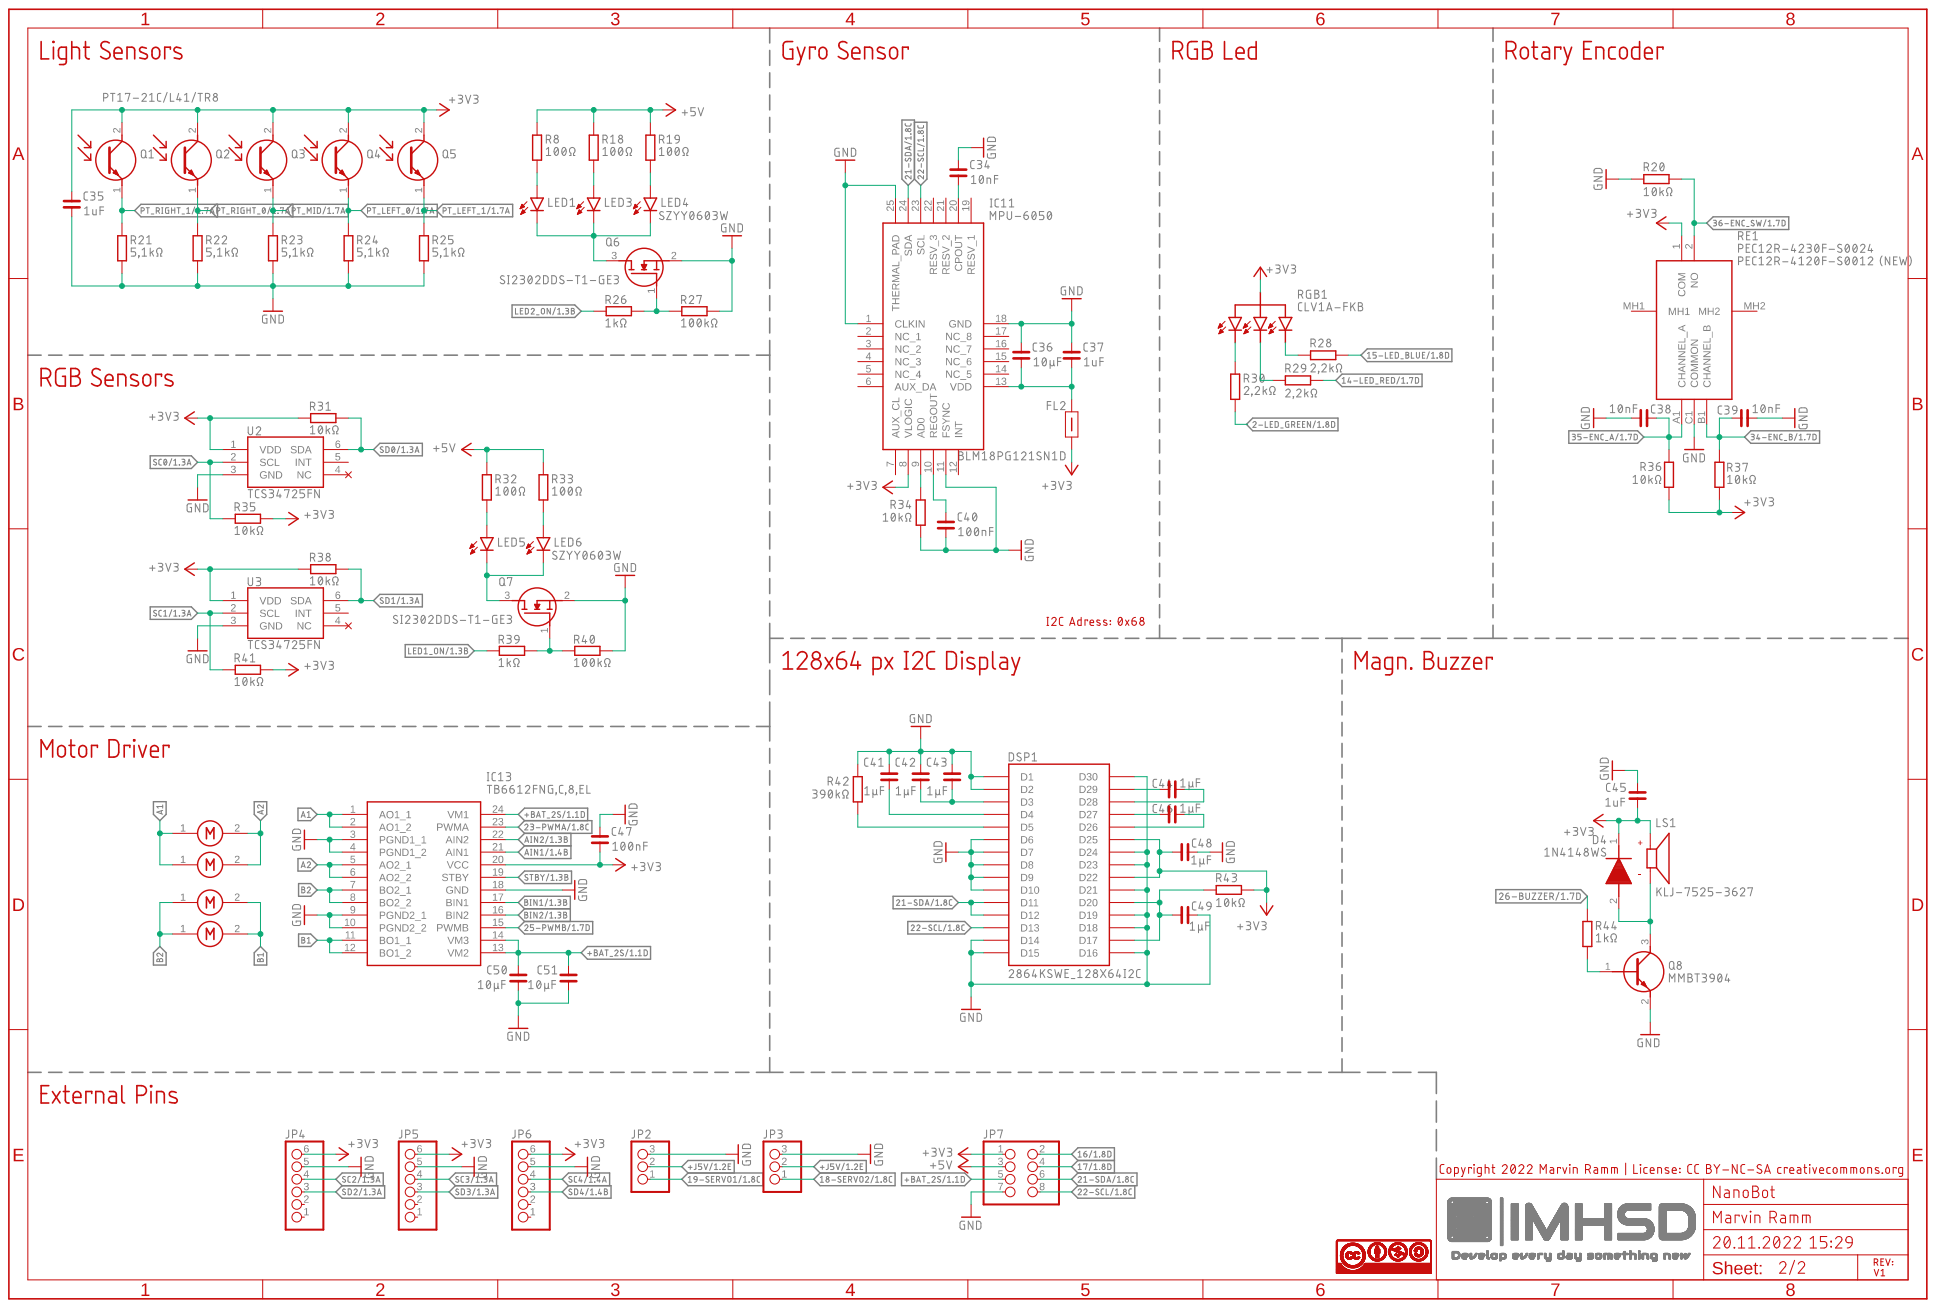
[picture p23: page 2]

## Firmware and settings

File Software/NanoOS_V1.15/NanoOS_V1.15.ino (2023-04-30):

       /////////////////////////////////////////////
      //                 NanoOS                  //
     //               Marvin Ramm               //
    //                REV: V1.15               //
   //     https://github.com/codemarv42/      //
  //        Last modified: 29.04.2023        //
 //      © Copyright 2023 CC-BY-NC-SA       //
/////////////////////////////////////////////

/*
   Arduino ESP32 Settings:
   Board: "ESP32 Dev Module"
   Upload Speed: "921600"
   CPU Frequency: "240MHz (WiFi/BT)"
   Flash Frequency: "80MHz"
   Flash Mode: "QIO"
   Flash Size: "16MB (128Mb)"
   Partition Scheme: "Minimal SPIFFS (1.9MB APP with OTA/190KB SPIFFS)"
   Programmer: "AVRISP mkll"
   Erase all flash: "Disabled"
*/

/*
   1. TO-DO:
   -Wumper testen und Rest
   -Contest Mode

   2. TO-DO:
   -Problem mit Kreuzung
   -Button drücken und Roboter resetten nur im Contest mode aktivieren
   -Dose Umfahren alle Fälle abdecken
   -Save cal Gyro data
   -Menupunkt zum herunterfahren des Roboters
   -Standby modus im Start menu
   -Contest Mode Überprüfen
   -Bezeichnungen der Abkürzungen für kal Werte ändern
   -Speicherung der Sensorwere MIN MAX außen + Prüfen ob kalibrierung funktioniert
   -Debug Modus anzeigen mit USB Symbol
   -Zurücksetzen des Programms mit einen Knopfdruck bsp wenn in einer Loop gefangen bsp im letztem Raum
*/

/*
   Stopped last:

*/

///////////////////Includes//////////////////

#include "Bitmap.h"
#include "Bluetooth.h"
#include "Display.h"
#include "ESP32_WiFi.h"
#include "Functions.h"
#include "Measure.h"
#include "Pins.h"
#include "Pitches.h"
#include "Settings.h"
#include "Tests.h"
#include "Tiles.h"

//////////////////Variables//////////////////


/////////////////////////////////////////////

////////////////////Setup////////////////////

void setup() {
  HardwareInit();

  //MotorTest();

  //Display Menu//

  if (CONTESTMODE == 0) {
    while (ENMainProgram == 0) {
      ReadEncoder();

      if (ENCCounter > 8) {
        ENCCounter = 8;
      }

      if (ENCCounter == 8) {
        MenuPage = 11;
      } else {
        MenuPage = ENCCounter;
      }

      MenuActions();
      OTALOOP();
    }
  } else {
    ENMainProgram = 1;
  }

  /*

  if (CalState == false) {
    TilesCase = 11;
    ForceDispUpdate = true;

    RGBOff();
    SetRGB(2,B);
    delay(3500);
    if (ENCButtonState == 1) {
      ENCButtonState = 0;
    } else {
      Calibrate(2500);
      PlayTone(0);
      delay(3000);
    }
    RGBOff();
  }

  */

  ShiftRegisterWrite(SR_LED_RGB, HIGH);
  ShiftRegisterWrite(SR_LED_PT, HIGH);
  VL53l1xInit(3, 2);
  delay(1500);
  RGBOff();
}

/////////////////////////////////////////////

////////////////////Loop/////////////////////

void loop() {
  if (DEBUGMODE == 1) {

    MeasureLight();
    PrintDataSerial(0);
    Serial.print("Core0 time:");
    Serial.print(Core0Time);
    Serial.println("ms");
    FollowLine(Normal);

  } else {

    if (!DEBUGRESCUE) {

      LoopState = 1;

      MeasureLight();

      CaseDistinction();

      if (WumperTime > millis()){
        RGBOff();
        SetRGB(2,R);
        TilesCase = 14;

        FollowLine(Wumper);
      }else{
        if (XAngle > 15) {  //Ramp up
        TilesCase = 9;
        RGBOff();
        SetRGB(2,G);
        SetRGB(2,B);

        FollowLine(Up);
      } else if (XAngle < -15) {  //Ramp down
        TilesCase = 10;
        RGBOff();
        SetRGB(2,R);
        SetRGB(2,B);

        FollowLine(Down);
      } else {  //Flat ground
        TilesCase = 0;
        RGBOff();
        SetRGB(2,B);

        FollowLine(Normal);
      }
      }

    } else {
      FindExit();
    }
  }
}

/////////////////////////////////////////////

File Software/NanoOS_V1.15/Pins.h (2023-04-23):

#ifndef PINS_H
#define PINS_H

#define EN_RST           17
#define P_ON             2

///////////ADC Multiplexer (CD74HC4067S)////////////

#define S0               4
#define S1               5
#define S2               12
#define S3               13
#define ADC_MULTI        39

#define ADC_PT_L_1       0
#define ADC_PT_L_0       1
#define ADC_PT_M         2
#define ADC_PT_R_0       3
#define ADC_PT_R_1       4
#define ADC_PT_L_2       5
#define ADC_PT_R_2       6
#define ADC_PT_REF       7
#define ADC_AE1          8 //External Analog Input
#define ADC_AE2          9 //External Analog Input


/////////////////////Servos/////////////////////////

#define SERVO1           19
#define SERVO2           18

/////////////Motor Driver (TB6612FNG)///////////////

#define PWMA             23
#define PWMB             25

////////////Shiftregister (74HC595PW)///////////////

#define SHCP             27
#define STCP             32
#define DS               33

//Shiftregister IC1

#define SR_AIN1          0
#define SR_AIN2          1
#define SR_BIN1          2
#define SR_BIN2          3
#define SR_STBY          4
#define SR_LED_RGB       5
#define SR_LED_PT        6
#define SR_LED_L_RED     7

//Shiftregister IC2

#define SR_LED_L_GREEN   8
#define SR_LED_L_BLUE    9
#define SR_LED_R_RED     10
#define SR_LED_R_GREEN   11
#define SR_LED_R_BLUE    12
#define SR_DE1           13 //External Digital Pins
#define SR_DE2           14 //External Digital Pins
#define SR_DE3           15 //External Digital Pins

/////////////////Rotary Encoder/////////////////////

#define ENC_A            35
#define ENC_B            34
#define ENC_SW           15

/////////////////////Buzzer/////////////////////////

#define BUZZER           26

////////////////////External////////////////////////

#define EXT1             16

/////////////////////Battery////////////////////////

#define VBAT             36
#define CHARGE_STAT      14 //NC in V2 because of no Voltage devider before Input Pin Voltage Overshoot about 1V!

//////////////////////I2C///////////////////////////

#define SDA              21
#define SCL              22
#define MPU6050_ADRESS   0x51
#define I2CMULTI_ADRESS  0x70
#define OLED_ADRESS      0x3C
#define TOF_ADRESS       0x29
#define RGBS_ADRESS      0x29


#endif

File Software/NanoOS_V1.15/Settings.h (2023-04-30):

#ifndef SETTINGS_H
#define SETTINGS_H

#define VERSION        1.15
#define MODELLNR       "DEV02"
#define DEBUGMODE      0 //0 - OFF, 1 - SET
#define CONTESTMODE    1 //0 - OFF, 1 - SET // If activated the robot will start directly the main program at boot
#define MANUALRGBVAL_G 0 //0 - OFF, 1 - SET // The calibrated green values are set manually
#define MANUALRGBVAL_R 0 //0 - OFF, 1 - SET // The calibrated red values are set manually
#define DEBUGRESCUE    0 //0 - OFF, 1 - SET // Starts the rescue program directly after start

//Engine speeds// At full battery charge!

#define Normal  110
#define Fast    150
#define Slow    80
#define Down    85
#define Up      90
#define Wumper  255

//Display//

#define SCREEN_WIDTH  128 // OLED display width, in pixels
#define SCREEN_HEIGHT 64 // OLED display height, in pixels
#define OLED_RESET    -1 // Reset pin # (or -1 if sharing Arduino reset pin)

#define FollowLineDiffFactor 4 //Integers only!

//Buzzer//

#define EN_BUZZER 1 //1 - ON, 0 - OFF

//Grayscale//

#define Grey   300
#define Black  150
#define White  850
#define Metal  1500
#define Green  450

//Other//

#define ObstacleDir 0 //0 - left, 1 - right

#endif

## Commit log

2022-11-30 Improvements and bug fixes
    -Bugs were fixed
    -RGB sensors can now be calibrated according to a color
    -Green is now reliably detected
    [Bluetooth.cpp, Display.cpp, ESP32_WiFi.cpp]
2022-12-18 New features and bug fixes
    [Bluetooth.cpp, Display.cpp, ESP32_WiFi.cpp]
2022-12-18 Bug Fixes
    -Accurate green detection
    -Accurate rotation by angle using the MPU6050
    [Bluetooth.cpp, Display.cpp, ESP32_WiFi.cpp]
2022-12-24 New functions
    -Calibrated values are stored correctly
    -Line search function was adjusted
    [Bluetooth.cpp, Display.cpp, ESP32_WiFi.cpp]
2023-03-05 New features and improvements
    -Bug fixes
    -Red calibration and detection
    -Calibrated red and green values can now be set manually
    -Improvement of the line search algorithm
    [Bluetooth.cpp, Display.cpp, ESP32_WiFi.cpp]
2023-03-11 Last program before the final competition
    -Find exit in the evacuation zone
    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
    [Bluetooth.cpp, Display.cpp, ESP32_WiFi.cpp]
